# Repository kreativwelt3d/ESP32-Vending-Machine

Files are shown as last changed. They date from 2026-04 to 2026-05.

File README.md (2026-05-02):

# Vending Machine Firmware (ESP32-S3)

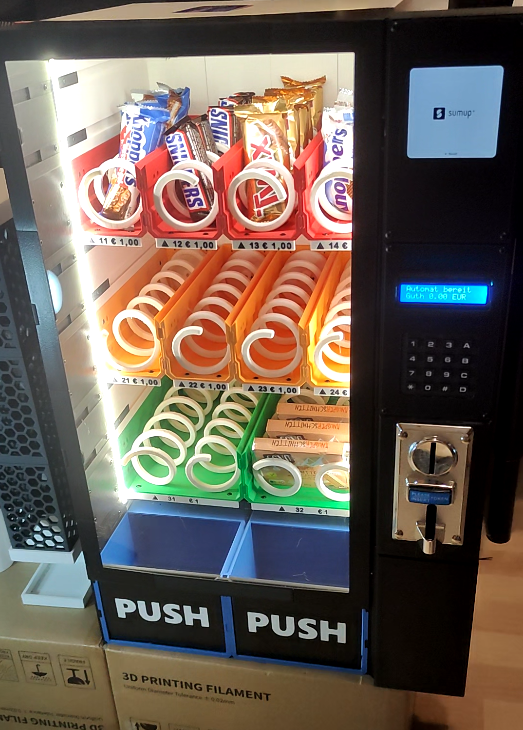
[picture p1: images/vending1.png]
Vending Machine


Language:

- [Deutsch](#deutsch)
- [English](#english)

Current firmware version in code: `1.7.0`

Ready-to-flash firmware releases are available here:

- https://github.com/kreativwelt3d/ESP32-Vending-Machine/releases

Kurzanleitung Flashen:

1. Fuer das [ESP Web Tool](https://espressif.github.io/esptool-js/) immer alle vier Dateien `bootloader.bin`, `partitions.bin`, `boot_app0.bin` und `firmware.bin` verwenden.
2. ESP32-S3 per USB verbinden.
3. Im ESP Web Tool mit `460800` Baud verbinden und `Flash Mode = DIO`, `Flash Frequency = 40m`, `Flash Size = 16MB` setzen.
4. Dateien mit diesen Offsets flashen: `bootloader.bin -> 0x0`, `partitions.bin -> 0x8000`, `boot_app0.bin -> 0xE000`, `firmware.bin -> 0x10000`.
5. Nach dem Flashen den ESP neu starten und den ersten Setup-Dialog auf dem LCD durchlaufen.

Quick flash guide:

1. For the [ESP Web Tool](https://espressif.github.io/esptool-js/), always use all four files: `bootloader.bin`, `partitions.bin`, `boot_app0.bin`, and `firmware.bin`.
2. Connect the ESP32-S3 via USB.
3. In the ESP Web Tool, connect with `460800` baud and set `Flash Mode = DIO`, `Flash Frequency = 40m`, and `Flash Size = 16MB`.
4. Flash the files with these offsets: `bootloader.bin -> 0x0`, `partitions.bin -> 0x8000`, `boot_app0.bin -> 0xE000`, `firmware.bin -> 0x10000`.
5. Reboot the ESP and complete the initial setup shown on the LCD.

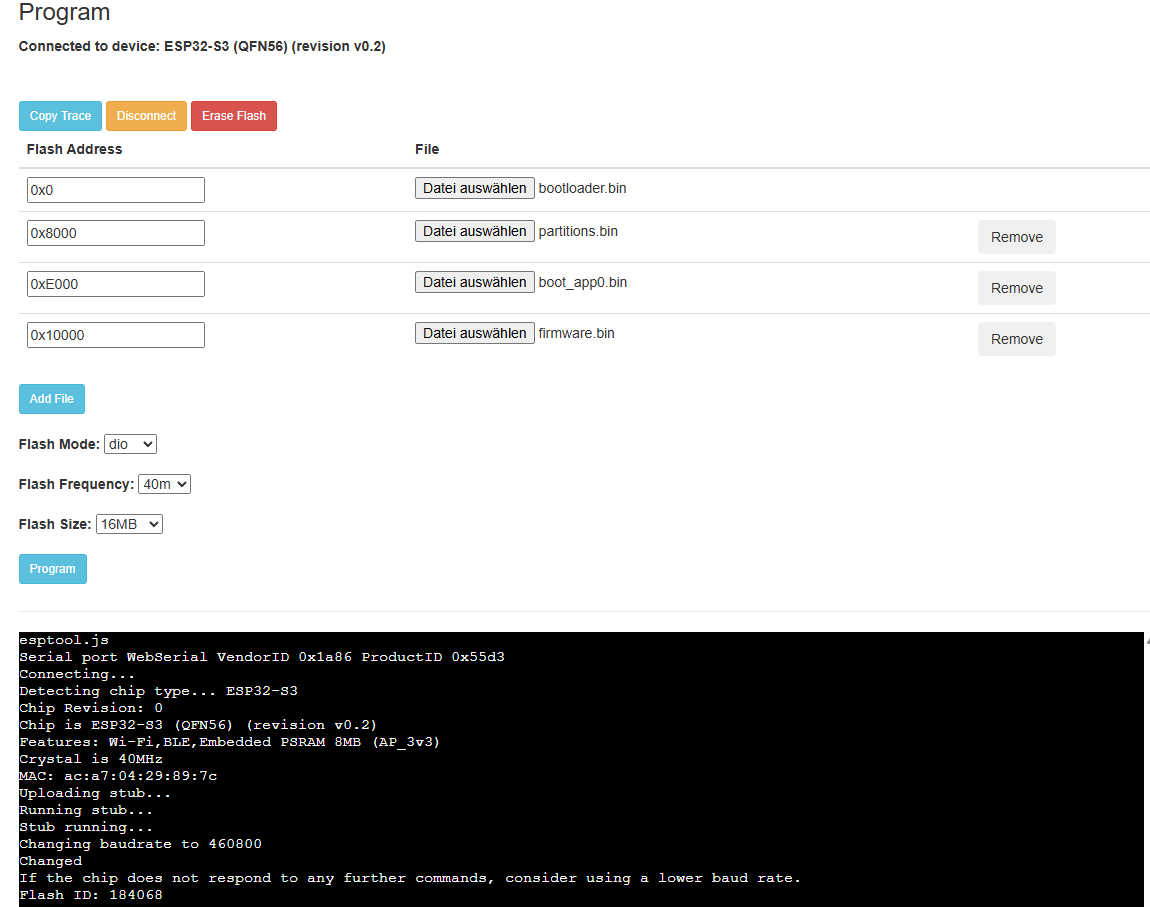
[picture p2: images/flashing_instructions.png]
Flashing instructions


---

## Deutsch

### Vorwort

Ein besonderer Dank geht an den Hauptschoepfer Martin auf MakerWorld fuer den grundlegenden Aufbau dieses Projekts und fuer das Bereitstellen der 3D-Druck-Dateien des Originalprojekts:

- https://makerworld.com/de/models/2380835-full-size-modular-vending-machine#profileId-2607127

Ausserdem begleitet eine TikTok-Videoreihe den kompletten Aufbau dieses Projekts. Die Links dazu koennen hier eingetragen werden:

Videoserie "Wir Drucken uns einen Verkaufsautomaten":
- Serien Start Teil 1: https://www.tiktok.com/@flo3137/video/7620130653631188246
- Aliexpress Lieferung + Unboxing Teil 2: https://www.tiktok.com/@flo3137/video/7622039398799904022
- Haupt aufbau des Automaten Teil 3: https://www.tiktok.com/@flo3137/video/7624063139864202518
- Elektronik Aufbau Teil 4: https://www.tiktok.com/@flo3137/video/7625582070978628867
- SumUP Mod + Finaler Teil: https://www.tiktok.com/@flo3137/video/7629085141201227031

Extra Videos:
- BL616 Münzprüfer Setup: https://www.tiktok.com/@flo3137/video/7628382295723887894

### Ueberblick

Diese Firmware steuert den Haupt-ESP eines Verkaufsautomaten. Der ESP32-S3 uebernimmt Anzeige, Tastenfeld, Muenzannahme, SD-Karte, WLAN/Weboberflaeche und die Kommunikation mit dem separaten Motor-ESP.

3D-Druck-Dateien und Hinweise zu den verfuegbaren Modifikationen findest du in [3DPrinting files/README.md](3DPrinting%20files/README.md).

### Funktionsumfang

- 4x4-Keypad fuer Bedienung und Service-Menue
- 16x2-LCD ueber I2C
- Erststart- und Service-Keypad-Setup zur Tasten-Zuordnung
- Muenzpruefer mit frei konfigurierbaren Puls/Wert-Mappings
- SD-Karte fuer Kassenbuch
- WLAN-Konfiguration
- Webserver fuer Konfiguration und Status
- Kommunikation mit separatem Motor-ESP per UART
- Ansteuerung von bis zu 24 Motoren ueber den separaten Motor-ESP
- Persistente Speicherung ueber Preferences (NVS)
- SumUp-Anbindung fuer Kartenzahlung
- Erstellung von Flash-Dateien fuer `esptool` und ESP Web Tool

### Hardware und Verdrahtung

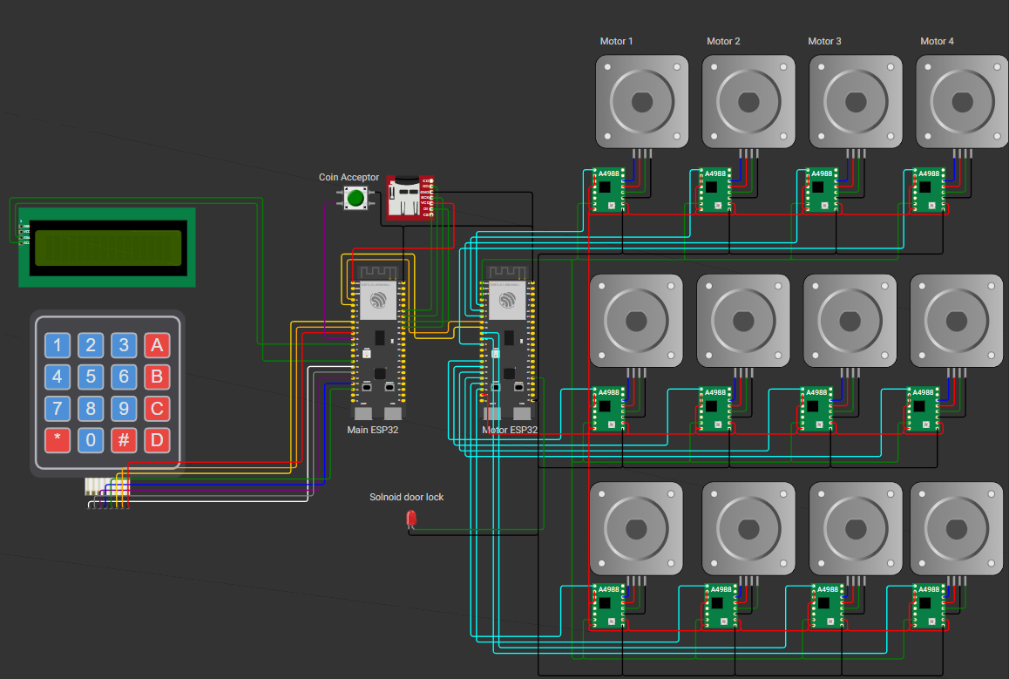
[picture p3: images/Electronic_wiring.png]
Aktuelle 5-Volt-Verdrahtung


*Aktuelle 5-Volt-Verdrahtung. Das Bild zeigt die komplette Verdrahtung aller Komponenten. Die 12V-Leitungen wurden bewusst weggelassen, um die Logik besser darzustellen.*

Alle aktuell in der Firmware belegten GPIOs:

| Funktion | Signal | GPIO |
|---|---|---|
| LCD I2C | SDA | `8` |
| LCD I2C | SCL | `9` |
| Keypad | Row 1 | `10` |
| Keypad | Row 2 | `11` |
| Keypad | Row 3 | `12` |
| Keypad | Row 4 | `13` |
| Keypad | Col 1 | `14` |
| Keypad | Col 2 | `15` |
| Keypad | Col 3 | `16` |
| Keypad | Col 4 | `17` |
| Muenzpruefer | Pulse input | `18` |
| Motor-ESP UART | TX vom Haupt-ESP | `4` |
| Motor-ESP UART | RX zum Haupt-ESP | `5` |
| SD-Karte SPI | SCK / CLK | `39` |
| SD-Karte SPI | MOSI / DI | `40` |
| SD-Karte SPI | MISO / DO | `41` |
| SD-Karte SPI | CS / SS | `42` |

Nicht aufgefuehrte GPIOs sind in der aktuellen Hauptplatinen-Firmware nicht belegt.

#### LCD

- Display: `16x2`
- I2C-Start im Code: `Wire.begin(8, 9)`
- Typische I2C-Adresse: `0x27`

Verdrahtung:

- `SDA -> GPIO 8`
- `SCL -> GPIO 9`
- `VCC -> 5V` oder `3.3V` je nach LCD-Backpack
- `GND -> GND`

Hinweis:

- Wenn das Display ueber I2C zu schwach leuchten sollte, kann zuerst der Kontrast ueber den Drehwiderstand am LCD-Backpack eingestellt werden.
- Falls das nicht ausreicht, kann statt `3.3V` auch `5V` fuer die Versorgung des Displays genutzt werden. Eventuell ist dann ein Level-Shifter zwischen `GPIO 8` und `GPIO 9` notwendig, um die ESP-Elektronik zu schuetzen.
- Die meisten LCD-Backpacks bringen diese Anpassung allerdings bereits von sich aus mit.

#### Keypad

Logische 4x4-Matrix:

| | Col 1 | Col 2 | Col 3 | Col 4 |
|---|---|---|---|---|
| Row 1 | 1 | 2 | 3 | A |
| Row 2 | 4 | 5 | 6 | B |
| Row 3 | 7 | 8 | 9 | C |
| Row 4 | * | 0 | # | D |

Physische Verdrahtung:

- `Row 1 -> GPIO 10`
- `Row 2 -> GPIO 11`
- `Row 3 -> GPIO 12`
- `Row 4 -> GPIO 13`
- `Col 1 -> GPIO 14`
- `Col 2 -> GPIO 15`
- `Col 3 -> GPIO 16`
- `Col 4 -> GPIO 17`

Hinweise:

- Beim ersten Start ohne gespeicherte Tasten-Zuordnung erscheint automatisch ein Keypad-Setup auf dem LCD.
- Das Setup kann spaeter erneut im Service-Menue ueber `Keypad Setup` gestartet werden.

#### Muenzpruefer

- Pulssignal-Eingang: `GPIO 18`
- Im Code als `INPUT_PULLUP` konfiguriert

Ein Video zum Einrichten des Muenzpruefers ist auf TikTok einsehbar:

- https://www.tiktok.com/@flo3137/video/7628382295723887894

Verdrahtung:

- `Signal / pulse out -> GPIO 18`
- `GND -> GND`

Hinweis:

- Wenn das Signal an `GPIO 18` zu schwach ist, kann es mit einem `10 kOhm`-Widerstand zwischen `5V` und `GPIO 18` verbessert werden.

#### SD-Karte

Die SD-Karte wird im SPI-Modus betrieben.

Aktuell funktionierende Verdrahtung:

- `CLK / SCK -> GPIO 39`
- `MOSI / DI -> GPIO 40`
- `MISO / DO -> GPIO 41`
- `CS / SS -> GPIO 42`
- `3V3 -> 3.3V`
- `GND -> GND`

Hinweise:

- Diese Belegung wurde erfolgreich getestet.
- Der testweise Pinblock `35/36/37/38` kann auf diesem Board zu Boot-Problemen fuehren.

#### Motor-ESP UART

Der Haupt-ESP kommuniziert mit dem separaten Motor-ESP ueber UART:

- `TX Haupt-ESP -> GPIO 4`
- `RX Haupt-ESP -> GPIO 5`
- Baudrate: `115200`

Verdrahtung:

- `GPIO 4` des Haupt-ESP an `RX` des Motor-ESP
- `GPIO 5` des Haupt-ESP an `TX` des Motor-ESP
- `GND` beider ESPs verbinden

Weitere Details zur Motor-Platine stehen in [motor_controller/README.md](motor_controller/README.md).

### Bedienkonzept

#### Wichtige Tasten

- `A` = Menue nach oben / Zeichensatz zurueck
- `B` = Menue nach unten / Zeichensatz weiter
- `C` = Zurueck / Abbrechen
- `D` = Bestaetigen / Enter
- `*` = Loeschen / Backspace
- `#` = regulaeres Eingabezeichen in Textfeldern

#### Service-Menue oeffnen

Wenn das Display auf "Automat bereit" steht, kann mit folgender nacheinander gedrücker Tasten `*` und `#` das Service-Menue geoeffnet werden.
Danach muss die Service-PIN eingegeben werden. Der standard Pin ist: `12345678`

#### Service-Menue

Aktuelle Menuepunkte:

1. `Info`
2. `WiFi`
3. `Admin PIN`
4. `Sprache`
5. `Keypad Setup`
6. `Tuer oeffnen`

#### WiFi-Text-Eingabe ueber das Keypad

Bei der Eingabe von `SSID` und `Passwort` wird eine Multi-Tap-Eingabe verwendet.

Bedienung:

- `A` = einen Zeichensatz zurueckschalten
- `B` = einen Zeichensatz weiterschalten
- `C` = Eingabe abbrechen und zurueck
- `D` = aktuelle Eingabe bestaetigen und speichern
- `*` = aktives Zeichen verwerfen oder letztes Zeichen loeschen
- Wenn dieselbe Zifferntaste mehrfach kurz hintereinander gedrueckt wird, wird durch die zugehoerigen Zeichen dieser Taste gewechselt
- Nach einer kurzen Pause wird das aktuell ausgewaehlte Zeichen uebernommen

Verfuegbare Zeichensaetze:

- `ABC` = Grossbuchstaben
- `abc` = Kleinbuchstaben
- `123` = Zahlen
- `Sym` = Sonderzeichen

Tastenbelegung:

- `0`
  Leerzeichen, `0` im Modus `ABC` und `abc`
  `0`, Leerzeichen, `@` im Modus `Sym`
  nur `0` im Modus `123`
- `1`
  `1 . - _` im Modus `ABC` und `abc`
  `1 .` im Modus `123`
  `. - _ /` im Modus `Sym`
- `2`
  `A B C 2` im Modus `ABC`
  `a b c 2` im Modus `abc`
  `2` im Modus `123`
  `# $ % &` im Modus `Sym`
- `3`
  `D E F 3` im Modus `ABC`
  `d e f 3` im Modus `abc`
  `3` im Modus `123`
  `* + = "` im Modus `Sym`
- `4`
  `G H I 4` im Modus `ABC`
  `g h i 4` im Modus `abc`
  `4` im Modus `123`
  `( ) , ;` im Modus `Sym`
- `5`
  `J K L 5` im Modus `ABC`
  `j k l 5` im Modus `abc`
  `5` im Modus `123`
  `: ! ? '` im Modus `Sym`
- `6`
  `M N O 6` im Modus `ABC`
  `m n o 6` im Modus `abc`
  `6` im Modus `123`
  `[ ] { }` im Modus `Sym`
- `7`
  `P Q R S 7` im Modus `ABC`
  `p q r s 7` im Modus `abc`
  `7` im Modus `123`
  `< > | \` im Modus `Sym`
- `8`
  `T U V 8` im Modus `ABC`
  `t u v 8` im Modus `abc`
  `8` im Modus `123`
  `^ ~ `` im Modus `Sym`
- `9`
  `W X Y Z 9` im Modus `ABC`
  `w x y z 9` im Modus `abc`
  `9` im Modus `123`
  `@` im Modus `Sym`
- `#`
  `#` in allen Zeichensaetzen

### Weboberflaeche

Der integrierte Webserver laeuft auf Port `80`.

Wichtige Bereiche:

- Uebersicht
- WiFi
- E-Mail
- SumUp
- Muenzen
- Schaechte
- Kassenbuch
- Tests

#### SumUp-Konfiguration

Im Tab `SumUp` werden die Parameter fuer die Kartenzahlung hinterlegt:

- `Aktiv`
- `Server Basis-URL`
- `Bearer Token`
- `Machine ID`
- `Currency`
- `Polling Intervall`
- `Timeout`

Beispiel fuer die `Server Basis-URL`:

```text
https://sumup.kreativwelt3d.de/sumup/public
```

Hinweise:

- Die Basis-URL muss auf den oeffentlich erreichbaren PHP-Bridge-Endpunkt zeigen.
- Der Bearer-Token schuetzt die Bridge-Endpunkte `/start` und `/status`.
- `Machine ID` muss mit dem Wert uebereinstimmen, den die Bridge fuer dieselbe Maschine erwartet.

#### SumUp API Bridge

Wenn du keine eigene SumUp API Bridge bauen und betreiben moechtest, kannst du die SumUp API Bridge auf meiner Webseite nutzen:

- https://sumup.kreativwelt3d.de/

Dieser Dienst kostet `5 EUR pro Monat` und kann nach der Anmeldung auf der Webseite ueber Stripe gebucht werden, wenn du keine eigene Bridge einsetzen willst.

Damit wird das Projekt mitfinanziert, und ich freue mich sehr, wenn du mit deiner Buchung dabei mithilfst.

Ueber den Dienst koennen dann beliebig viele SumUp-Terminals angebunden werden.

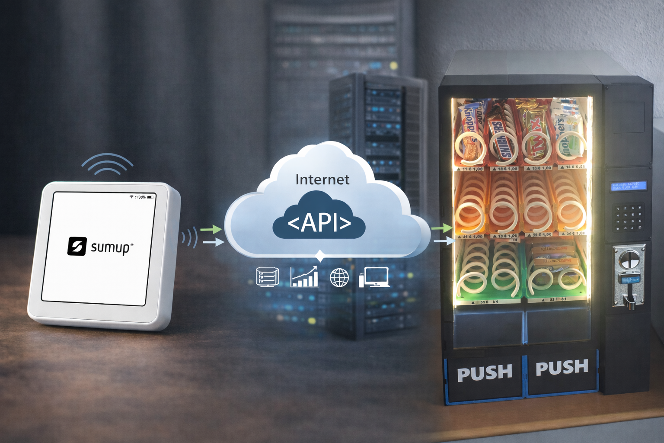
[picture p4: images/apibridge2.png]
SumUp API Bridge


#### Produkt- und Kartenzahlungsablauf

Die Produktauswahl am 4x4-Keypad erfolgt zweistufig:

- zuerst `Reihe 1-6`
- danach `Fach 1-8`

Beispiel:

- `1` dann `2` = Reihe 1, Fach 2

Wenn genuegend Guthaben vorhanden ist:

- Das Produkt wird direkt ausgegeben.

Wenn Guthaben fehlt und SumUp korrekt konfiguriert ist:

- Das LCD zeigt `Kartenzahlung->A`
- mit `A` wird die Kartenzahlung fuer genau diesen Artikel gestartet
- das LCD zeigt anschliessend `Terminal beachten`
- nach erfolgreicher Transaktion wird die Ware automatisch ausgegeben
- bei fehlgeschlagener oder abgebrochener Zahlung erfolgt keine Ausgabe

Wichtig:

- `A` startet im Normalmodus keine freie Betragsaufladung mehr.
- Die Kartenzahlung ist direkt an den ausgewaehlten Artikel gekoppelt.

#### Muenzkonfiguration

- Frei konfigurierbare Puls/Wert-Mappings
- Bis zu `20` Eintraege
- Weboberflaeche mit `Eintrag hinzufuegen` und `Eintrag entfernen`

#### Login

- Login mit Service-/Admin-PIN
- Session-Cookie: `ESPSESSIONID`

### Persistente Einstellungen

Namespace: `vending`

Gespeichert werden unter anderem:

- Admin-PIN
- WLAN-Daten
- Sprache
- Waehrung
- Keypad-Zuordnung
- Muenz-Mappings
- E-Mail-Konfiguration
- Schacht-Konfiguration

### Setup und Inbetriebnahme

1. Board `esp32-s3-devkitc-1-n16r8` in PlatformIO verwenden.
2. Firmware mit `platformio run` bauen.
3. Fuer das ESP Web Tool nicht die gemergte Datei `firmware-merged.bin` verwenden, sondern die vier Einzeldateien aus `.pio/build/esp32-s3-devkitc-1/`.
4. Im ESP Web Tool mit `460800` Baud verbinden und `Flash Mode = DIO`, `Flash Frequency = 40m`, `Flash Size = 16MB` setzen.
5. Dateien mit diesen Offsets flashen: `bootloader.bin -> 0x0`, `partitions.bin -> 0x8000`, `boot_app0.bin -> 0xE000`, `firmware.bin -> 0x10000`.
6. Seriellen Monitor mit `115200` Baud oeffnen.
7. Beim Erststart gegebenenfalls das Keypad-Setup auf dem LCD durchlaufen.
8. SD-Karte und WLAN pruefen.
9. Service-Menue und Weboberflaeche fuer weitere Konfiguration verwenden.

### Fehlersuche

#### SD-Karte wird nicht erkannt

- Verdrahtung fuer `GPIO 39/40/41/42` pruefen
- `3.3V` und `GND` pruefen
- Seriellen Monitor beobachten

#### Keypad reagiert falsch

- `Keypad Setup` im Service-Menue erneut ausfuehren
- Verdrahtung von Rows und Cols pruefen

#### Kein Zugriff auf die Webseite

- WLAN-Verbindung pruefen
- IP-Adresse im Info-Screen oder seriellen Monitor nachsehen
- Browser im selben Netzwerk verwenden

### Sicherheit und Grenzen

- Authentifizierung erfolgt ueber PIN und Session-Cookie
- Kein HTTPS/TLS in der aktuellen Firmware
- Fuer produktive Umgebungen sollte ein zusaetzliches Sicherheitskonzept ergaenzt werden

---

## English

### Preface

Special thanks go to Martin on MakerWorld, the main creator of the original build, for creating the foundation of this project and for providing the 3D printing files of the original project:

- https://makerworld.com/de/models/2380835-full-size-modular-vending-machine#profileId-2607127

In addition, a TikTok video series documents the complete build of this project the Series is held upon in German.Maybe i can add some english voiceover later on:

Videoseries "We print an vending machine":
- Series start part 1: https://www.tiktok.com/@flo3137/video/7620130653631188246
- Aliexpress delivered + Unboxing part 2: https://www.tiktok.com/@flo3137/video/7622039398799904022
- Main build of the vendingmachine part 3: https://www.tiktok.com/@flo3137/video/7624063139864202518
- Electronics part 4: https://www.tiktok.com/@flo3137/video/7625582070978628867
- SumUP Mod + Final part: https://www.tiktok.com/@flo3137/video/7629085141201227031

Extra Videos:
- BL616 Coin acceptor Setup: https://www.tiktok.com/@flo3137/video/7628382295723887894

### Overview

This firmware controls the main ESP of the vending machine. The ESP32-S3 handles the display, keypad, coin acceptor, SD card, Wi-Fi/web interface, and communication with the separate motor ESP.

3D printing files and notes about the available modifications can be found in [3DPrinting files/README.md](3DPrinting%20files/README.md).

### Features

- 4x4 keypad for normal operation and service menu
- 16x2 LCD via I2C
- Initial and service keypad setup for key mapping
- Coin acceptor with configurable pulse/value mappings
- SD card support for the cashbook
- Wi-Fi configuration
- Web server for configuration and status pages
- UART communication with a separate motor ESP
- Control of up to 24 motors through the separate motor ESP
- Persistent storage via Preferences (NVS)
- SumUp integration for card payments
- Automatic creation of flash files for `esptool` and ESP Web Tool

### Hardware and wiring

Current 5-volt wiring

*Current 5-volt wiring. The image shows the complete wiring of all components. The 12V lines were intentionally omitted to make the logic easier to understand.*

GPIOs currently used by the firmware:

| Function | Signal | GPIO |
|---|---|---|
| LCD I2C | SDA | `8` |
| LCD I2C | SCL | `9` |
| Keypad | Row 1 | `10` |
| Keypad | Row 2 | `11` |
| Keypad | Row 3 | `12` |
| Keypad | Row 4 | `13` |
| Keypad | Col 1 | `14` |
| Keypad | Col 2 | `15` |
| Keypad | Col 3 | `16` |
| Keypad | Col 4 | `17` |
| Coin acceptor | Pulse input | `18` |
| Motor ESP UART | TX from main ESP | `4` |
| Motor ESP UART | RX to main ESP | `5` |
| SD card SPI | SCK / CLK | `39` |
| SD card SPI | MOSI / DI | `40` |
| SD card SPI | MISO / DO | `41` |
| SD card SPI | CS / SS | `42` |

Unlisted GPIOs are currently unused by the main board firmware.

For the motor ESP pin mapping, see [motor_controller/README.md](motor_controller/README.md).

### User interaction

Important keys:

- `A` = menu up / previous character set
- `B` = menu down / next character set
- `C` = back / cancel
- `D` = confirm / enter
- `*` = delete / backspace
- `#` = regular input character in text fields

If the display shows "Machine ready" then the service menu is opened by pressing `*` and `#` quickly one after another, then entering the service PIN. The service pin is `12345678`

Current service menu items:

1. `Info`
2. `WiFi`
3. `Admin PIN`
4. `Language`
5. `Keypad Setup`
6. `Open door`

#### WiFi text input via keypad

When entering `SSID` and `password`, the firmware uses a multi-tap text input.

Controls:

- `A` = switch to the previous character set
- `B` = switch to the next character set
- `C` = cancel input and go back
- `D` = confirm and save the current input
- `*` = discard the active character or delete the last committed character
- Pressing the same number key multiple times quickly cycles through the characters assigned to that key
- After a short pause, the currently selected character is committed

Available character sets:

- `ABC` = uppercase letters
- `abc` = lowercase letters
- `123` = numbers
- `Sym` = symbols

Key mapping:

- `0`
  space, `0` in `ABC` and `abc`
  space, `0`, `@` in `Sym`
  only `0` in `123`
- `1`
  `1 . - _` in `ABC` and `abc`
  `1 .` in `123`
  `. - _ /` in `Sym`
- `2`
  `A B C 2` in `ABC`
  `a b c 2` in `abc`
  `2` in `123`
  `# $ % &` in `Sym`
- `3`
  `D E F 3` in `ABC`
  `d e f 3` in `abc`
  `3` in `123`
  `* + = "` in `Sym`
- `4`
  `G H I 4` in `ABC`
  `g h i 4` in `abc`
  `4` in `123`
  `( ) , ;` in `Sym`
- `5`
  `J K L 5` in `ABC`
  `j k l 5` in `abc`
  `5` in `123`
  `: ! ? '` in `Sym`
- `6`
  `M N O 6` in `ABC`
  `m n o 6` in `abc`
  `6` in `123`
  `[ ] { }` in `Sym`
- `7`
  `P Q R S 7` in `ABC`
  `p q r s 7` in `abc`
  `7` in `123`
  `< > | \` in `Sym`
- `8`
  `T U V 8` in `ABC`
  `t u v 8` in `abc`
  `8` in `123`
  `^ ~ `` in `Sym`
- `9`
  `W X Y Z 9` in `ABC`
  `w x y z 9` in `abc`
  `9` in `123`
  `@` in `Sym`
- `#`
  `#` in all character sets

### Web interface

The integrated web server runs on port `80`.

Main sections:

- Overview
- WiFi
- Email
- SumUp
- Coins
- Shafts
- Cashbook
- Tests

#### SumUp configuration

The `SumUp` tab contains the parameters for card payments:

- `Active`
- `Server base URL`
- `Bearer token`
- `Machine ID`
- `Currency`
- `Polling interval`
- `Timeout`

Example base URL:

```text
https://sumup.kreativwelt3d.de/sumup/public
```

#### SumUp API Bridge

If you do not want to build and host your own SumUp API bridge, you can use the SumUp API bridge on my website:

- https://sumup.kreativwelt3d.de/

This service costs `EUR 5 per month` and can be booked via Stripe after signing up on the website if you do not want to run your own bridge.

This helps fund the project, and I really appreciate everyone who supports it by subscribing to the service.

The service can be used to connect an unlimited number of SumUp terminals.

SumUp API Bridge

#### Product and card payment flow

Product selection on the 4x4 keypad is a two-step process:

- first `row 1-6`
- then `slot 1-8`

Example:

- `1` then `2` = row 1, slot 2

If enough credit is available:

- The product is dispensed immediately.

If there is not enough credit and SumUp is configured correctly:

- the LCD shows `Kartenzahlung->A`
- pressing `A` starts card payment for exactly that item
- the LCD then shows `Terminal beachten`
- after a successful transaction, the product is dispensed automatically
- no product is dispensed if the payment fails or is cancelled

### Persistent settings

Namespace: `vending`

Stored values include:

- admin PIN
- Wi-Fi settings
- language
- currency
- keypad mapping
- coin mappings
- email configuration
- shaft configuration

### Build and flashing

1. Use board `esp32-s3-devkitc-1-n16r8` in PlatformIO.
2. Build with `platformio run`.
3. For the ESP Web Tool, do not use the merged image `firmware-merged.bin`; use the four separate files from `.pio/build/esp32-s3-devkitc-1/` instead.
4. In the ESP Web Tool, connect with `460800` baud and set `Flash Mode = DIO`, `Flash Frequency = 40m`, and `Flash Size = 16MB`.
5. Flash the files with these offsets: `bootloader.bin -> 0x0`, `partitions.bin -> 0x8000`, `boot_app0.bin -> 0xE000`, `firmware.bin -> 0x10000`.
6. Open the serial monitor at `115200` baud.
7. Run the LCD keypad setup on first boot if needed.
8. Check SD card and Wi-Fi.
9. Use the service menu and web UI for further configuration.

### Troubleshooting

#### SD card is not detected

- Check wiring for `GPIO 39/40/41/42`
- Check `3.3V` and `GND`
- Watch the serial monitor output

#### Keypad behaves incorrectly

- Run `Keypad Setup` again from the service menu
- Check row and column wiring

#### Web interface is not reachable

- Check the Wi-Fi connection
- Look up the IP address on the info screen or in the serial monitor
- Make sure the browser is on the same network

### Security and limitations

- Authentication uses a PIN and session cookie
- No HTTPS/TLS in the current firmware
- A dedicated security concept is recommended for production environments

---

Notes:

- This README describes the main board firmware in `main_esp/src/sketch.ino`.
- The motor controller board has its own firmware and documentation in `motor_controller`.

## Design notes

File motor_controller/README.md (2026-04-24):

# Motor ESP Pinout

Language:

- [Deutsch](#deutsch)
- [English](#english)

---

## Deutsch

Diese Firmware in `src/main.cpp` ist fuer einen separaten ESP32-S3 als Motor-Controller gedacht.

Der Motor-ESP uebernimmt:

- 24 Stepper-Treiber ueber gemeinsame `STEP`-Leitung
- individuelle `ENABLE`-Leitungen pro Treiber
- Magnetschloss
- UART-Kommunikation mit dem Haupt-ESP

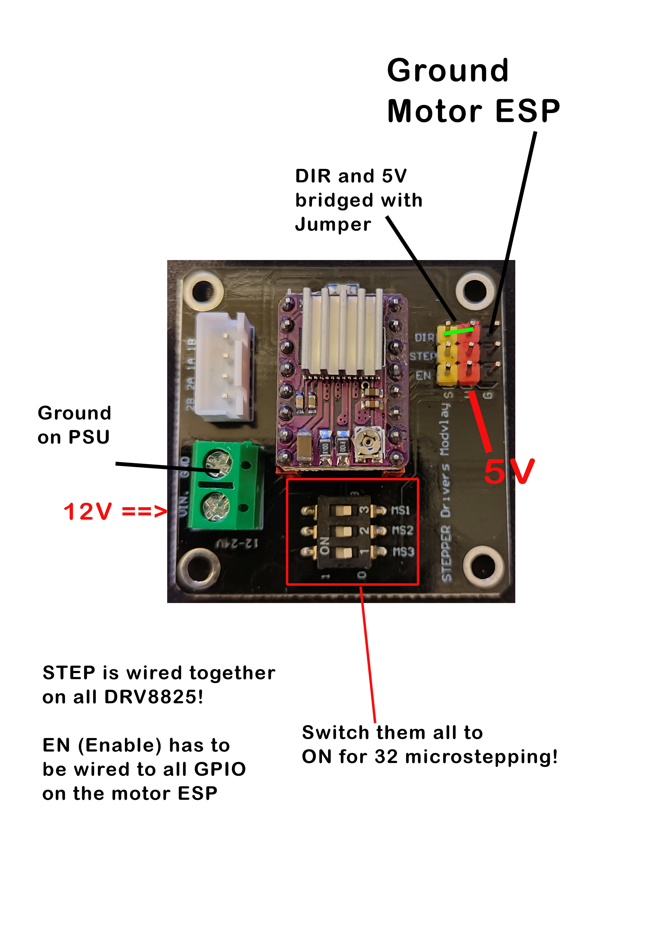
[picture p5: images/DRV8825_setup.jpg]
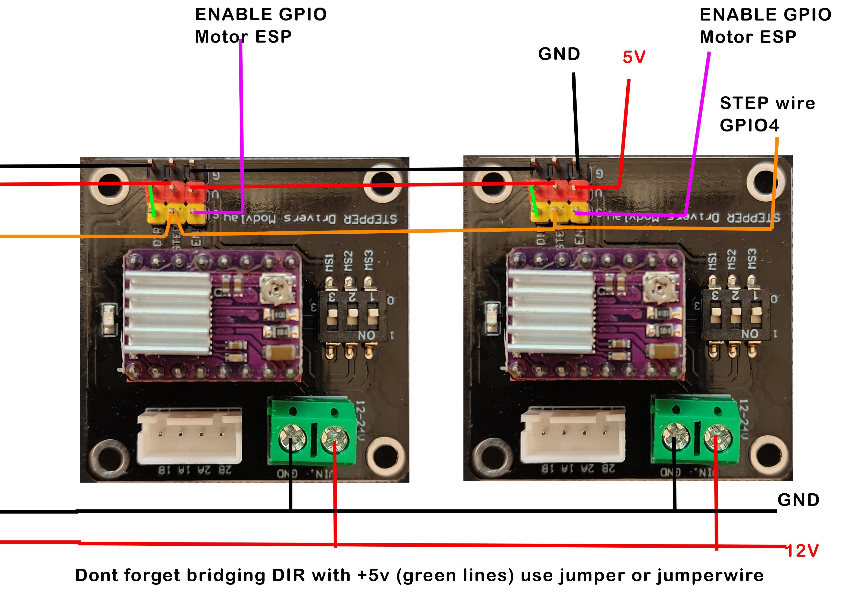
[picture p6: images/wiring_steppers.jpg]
  

Motor ESP wiring

## UART zum Haupt-ESP

Aktuelle Konfiguration im Sketch:

- Motor-ESP `RX`: `GPIO15`
- Motor-ESP `TX`: `GPIO16`
- Baudrate: `115200`

Verdrahtung:

- Haupt-ESP `TX` -> Motor-ESP `RX (GPIO15)`
- Haupt-ESP `RX` <- Motor-ESP `TX (GPIO16)`
- `GND` beider ESPs verbinden

## Stepper-Pins

Gemeinsame `STEP`-Leitung:

- `GPIO4`

`ENABLE`-Leitungen der 24 Motoren:

1. Motor 1: `GPIO5`
2. Motor 2: `GPIO6`
3. Motor 3: `GPIO7`
4. Motor 4: `GPIO8`
5. Motor 5: `GPIO9`
6. Motor 6: `GPIO10`
7. Motor 7: `GPIO11`
8. Motor 8: `GPIO12`
9. Motor 9: `GPIO13`
10. Motor 10: `GPIO14`
11. Motor 11: `GPIO17`
12. Motor 12: `GPIO18`
13. Motor 13: `GPIO1`
14. Motor 14: `GPIO2`
15. Motor 15: `GPIO38`
16. Motor 16: `GPIO39`
17. Motor 17: `GPIO40`
18. Motor 18: `GPIO41`
19. Motor 19: `GPIO42`
20. Motor 20: `GPIO47`
21. Motor 21: `GPIO48`
22. Motor 22: `GPIO19`
23. Motor 23: `GPIO20`
24. Motor 24: `GPIO3`

Logik:

- `ENABLE` aktiv: `LOW`
- `ENABLE` inaktiv: `HIGH`

## Magnetschloss

- Schloss-Pin: `GPIO21`
- aktiv/offen: `HIGH`
- inaktiv/geschlossen: `LOW`

Standard-Pulsdauer:

- `5000 ms`

## Hinweise zur Verdrahtung

- Alle DRV8825-Treiber muessen eine gemeinsame `GND` mit dem Motor-ESP haben.
- Die gemeinsame `STEP`-Leitung geht an alle Treiber parallel.
- Jeder Treiber bekommt seine eigene `ENABLE`-Leitung.
- Aktuelle Motor-zu-Pin-Zuordnung: Motor 1->GPIO5, Motor 2->GPIO6, Motor 3->GPIO7, Motor 4->GPIO8, Motor 5->GPIO9, Motor 6->GPIO10, Motor 7->GPIO11, Motor 8->GPIO12, Motor 9->GPIO13, Motor 10->GPIO14, Motor 11->GPIO17, Motor 12->GPIO18, Motor 13->GPIO1, Motor 14->GPIO2, Motor 15->GPIO38, Motor 16->GPIO39, Motor 17->GPIO40, Motor 18->GPIO41, Motor 19->GPIO42, Motor 20->GPIO47, Motor 21->GPIO48, Motor 22->GPIO19, Motor 23->GPIO20, Motor 24->GPIO3.
- Wenn `DIR` ebenfalls ueber den Motor-ESP laufen soll, muss der Sketch erweitert werden. Aktuell unterstuetzt der Motor-ESP nur `STEP + ENABLE` entsprechend dem bestehenden Projektansatz.

## Relevante Stellen im Code

- Pin-Konfiguration: `src/main.cpp`
- Protokollbeschreibung: `PROTOCOL.md`

---

## English

This firmware in `src/main.cpp` is intended for a separate ESP32-S3 used as the motor controller.

The motor ESP handles:

- 24 stepper drivers through a shared `STEP` line
- individual `ENABLE` lines for each driver
- magnetic lock
- UART communication with the main ESP

  

Motor ESP wiring

## UART to the main ESP

Current configuration in the sketch:

- Motor ESP `RX`: `GPIO15`
- Motor ESP `TX`: `GPIO16`
- Baud rate: `115200`

Wiring:

- Main ESP `TX` -> Motor ESP `RX (GPIO15)`
- Main ESP `RX` <- Motor ESP `TX (GPIO16)`
- Connect `GND` between both ESPs

## Stepper pins

Shared `STEP` line:

- `GPIO4`

`ENABLE` lines for the 24 motors:

1. Motor 1: `GPIO5`
2. Motor 2: `GPIO6`
3. Motor 3: `GPIO7`
4. Motor 4: `GPIO8`
5. Motor 5: `GPIO9`
6. Motor 6: `GPIO10`
7. Motor 7: `GPIO11`
8. Motor 8: `GPIO12`
9. Motor 9: `GPIO13`
10. Motor 10: `GPIO14`
11. Motor 11: `GPIO17`
12. Motor 12: `GPIO18`
13. Motor 13: `GPIO1`
14. Motor 14: `GPIO2`
15. Motor 15: `GPIO38`
16. Motor 16: `GPIO39`
17. Motor 17: `GPIO40`
18. Motor 18: `GPIO41`
19. Motor 19: `GPIO42`
20. Motor 20: `GPIO47`
21. Motor 21: `GPIO48`
22. Motor 22: `GPIO19`
23. Motor 23: `GPIO20`
24. Motor 24: `GPIO3`

Logic:

- `ENABLE` active: `LOW`
- `ENABLE` inactive: `HIGH`

## Magnetic lock

- Lock pin: `GPIO21`
- active/open: `HIGH`
- inactive/closed: `LOW`

Default pulse duration:

- `5000 ms`

## Wiring notes

- All DRV8825 drivers must share `GND` with the motor ESP.
- The shared `STEP` line goes to all drivers in parallel.
- Each driver gets its own `ENABLE` line.
- Current motor-to-pin mapping: Motor 1->GPIO5, Motor 2->GPIO6, Motor 3->GPIO7, Motor 4->GPIO8, Motor 5->GPIO9, Motor 6->GPIO10, Motor 7->GPIO11, Motor 8->GPIO12, Motor 9->GPIO13, Motor 10->GPIO14, Motor 11->GPIO17, Motor 12->GPIO18, Motor 13->GPIO1, Motor 14->GPIO2, Motor 15->GPIO38, Motor 16->GPIO39, Motor 17->GPIO40, Motor 18->GPIO41, Motor 19->GPIO42, Motor 20->GPIO47, Motor 21->GPIO48, Motor 22->GPIO19, Motor 23->GPIO20, Motor 24->GPIO3.
- If `DIR` should also be controlled by the motor ESP, the sketch needs to be extended. At the moment the motor ESP only supports `STEP + ENABLE` based on the current project design.

## Relevant code locations

- Pin configuration: `src/main.cpp`
- Protocol description: `PROTOCOL.md`

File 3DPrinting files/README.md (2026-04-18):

# 3D Printing Files

## Deutsch

Die 3D-Dateien in diesem Ordner sind Modifikationen und Erweiterungen fuer das offizielle MakerWorld-Projekt von Martin.

Das Originalprojekt findest du hier:

- https://makerworld.com/de/models/2380835-full-size-modular-vending-machine#profileId-2607127

Die auf MakerWorld gehosteten Modifikationen findest du hier:

- https://makerworld.com/de/models/2678974-sumup-solo-terminal-mod-esp23-new-housing#profileId-2966622

Ein weiteres MakerWorld-Projekt fuer die Modifikationen rund um den Motor-ESP und den Bereich unter dem Geraet findest du hier:

- https://makerworld.com/de/models/2624323-esp32-keypad-housing-backplate-modification#profileId-2897053

Bitte beachte, dass diese Dateien nicht das originale Basisprojekt ersetzen, sondern als angepasste Zusatz- oder Umbau-Teile dafuer gedacht sind. Die Modifikationen in diesem Repository und die MakerWorld-Versionen werden parallel gepflegt. Die Dateien aus dem Projekt fuer Motor-ESP und Unterseite sind ebenfalls in diesem GitHub-Repository enthalten.

## English

The 3D files in this folder are modifications and add-ons for Martin's official MakerWorld project.

You can find the original project here:

- https://makerworld.com/de/models/2380835-full-size-modular-vending-machine#profileId-2607127

The MakerWorld-hosted modifications are available here:

- https://makerworld.com/de/models/2678974-sumup-solo-terminal-mod-esp23-new-housing#profileId-2966622

Another MakerWorld project for the motor ESP modifications and the parts mounted underneath the machine is available here:

- https://makerworld.com/de/models/2624323-esp32-keypad-housing-backplate-modification#profileId-2897053

Please note that these files do not replace the original base project. They are intended as custom additional or modified parts for it. The modifications in this repository and the MakerWorld versions are maintained in parallel. The files from the motor ESP and bottom-side project are also included in this GitHub repository.

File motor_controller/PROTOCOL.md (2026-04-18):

# UART Protocol

Der Haupt-ESP bleibt Master. Der Motor-ESP fuehrt nur niederwertige Aktoren aus:

- 24 Stepper-Treiber ueber gemeinsame `STEP`-Leitung und individuelle `ENABLE`
- Magnetschloss

## Transport

- Physikalisch: UART
- Baudrate: `115200`
- Verdrahtung:
  - Haupt-ESP `TX` -> Motor-ESP `RX`
  - Haupt-ESP `RX` <- Motor-ESP `TX`
  - gemeinsame `GND`
- Nachrichtenformat: ASCII, eine Zeile pro Frame, `\n` als Abschluss

## Frame-Format

Request:

```text
@<id> <CMD> [args...]
```

Response:

```text
@<id> OK [payload...]
@<id> ERR <code> [details...]
```

Asynchrone Events:

```text
!READY fw=motor-esp-v2
!BUSY <id> <task>
!DONE <id>
!LOCK open duration_ms=<n>
```

Die `id` kommt vom Haupt-ESP und erlaubt Korrelation von Request und Response.

## Befehle

`PING`

```text
@1 PING
@1 OK PONG
```

`INFO`

```text
@2 INFO
@2 OK fw=motor-esp-v2 motors=24 step_pin=4 lock_pin=21
```

`STATUS`

```text
@3 STATUS
@3 OK busy=0 door=closed
```

`OFF`

```text
@4 OFF
@4 OK motors=off
```

`TEST <motor> <steps> <pulse_us>`

- `motor`: 1..24
- `steps`: 1..12000
- `pulse_us`: 100..5000

```text
@5 TEST 3 200 800
@5 OK motors=3 steps=200 pulse_us=800
```

`RUN <mask> <steps> <pulse_us>`

- `mask` ist eine Bitmaske fuer Motoren 1..24
- Bit 0 = Motor 1
- Bit 1 = Motor 2
- ...
- Bit 23 = Motor 24

Beispiel: Motor 9 und 10 gemeinsam

```text
@6 RUN 0x300 3200 800
@6 OK motors=9,10 steps=3200 pulse_us=800
```

Motor-zu-Pin-Zuordnung auf dem Motor-ESP:

- Motor 1=`GPIO5`, Motor 2=`GPIO6`, Motor 3=`GPIO7`, Motor 4=`GPIO8`
- Motor 5=`GPIO9`, Motor 6=`GPIO10`, Motor 7=`GPIO11`, Motor 8=`GPIO12`
- Motor 9=`GPIO13`, Motor 10=`GPIO14`, Motor 11=`GPIO17`, Motor 12=`GPIO18`
- Motor 13=`GPIO1`, Motor 14=`GPIO2`, Motor 15=`GPIO38`, Motor 16=`GPIO39`
- Motor 17=`GPIO40`, Motor 18=`GPIO41`, Motor 19=`GPIO42`, Motor 20=`GPIO47`
- Motor 21=`GPIO48`, Motor 22=`GPIO19`, Motor 23=`GPIO20`, Motor 24=`GPIO3`

`LOCK [duration_ms]`

- Standard ohne Argument: `5000`

```text
@7 LOCK 5000
!BUSY 7 LOCK
!LOCK open duration_ms=5000
@7 OK lock=closed
!DONE 7
```

## Fehlercodes

- `BAD_FRAME`
- `BAD_CMD`
- `BAD_ARGS`
- `BUSY`
- `BAD_MOTOR`
- `RUN_FAIL`
- `TEST_FAIL`
- `LOCK_FAIL`

## Architekturentscheidung

Die Schachtlogik bleibt auf dem Haupt-ESP:

- Zuordnung Schacht -> Motor(e)
- Preislogik
- Bestandslogik
- Webserver
- WLAN

Der Motor-ESP kennt nur generische Aktionen:

- einen oder mehrere Motoren mit Schrittzahl/Pulsweite fahren
- Magnetschloss pulsen

Dadurch bleibt der Motor-ESP einfach und testbar.

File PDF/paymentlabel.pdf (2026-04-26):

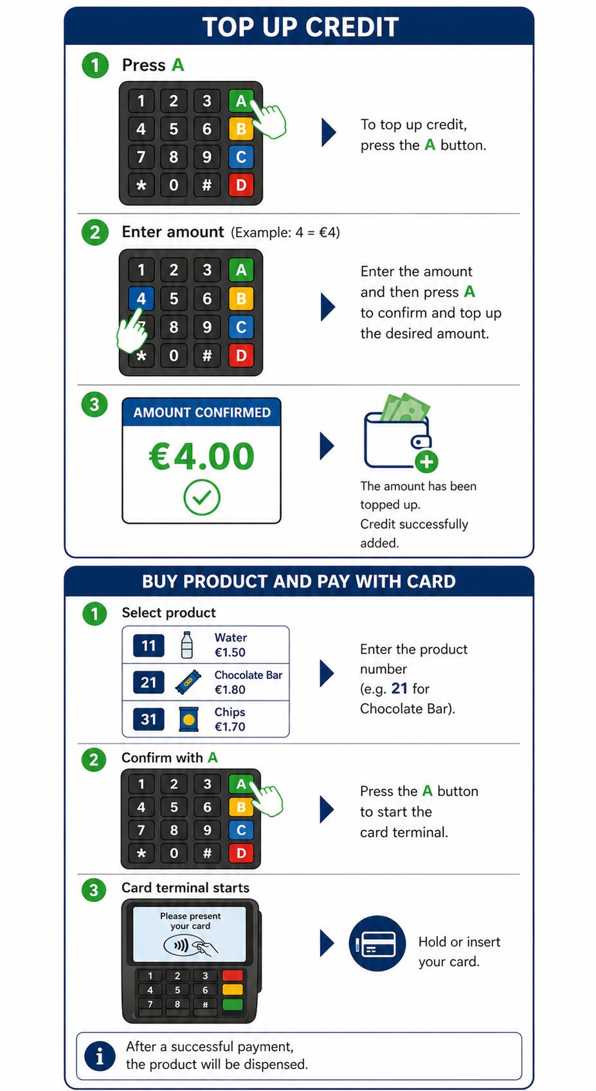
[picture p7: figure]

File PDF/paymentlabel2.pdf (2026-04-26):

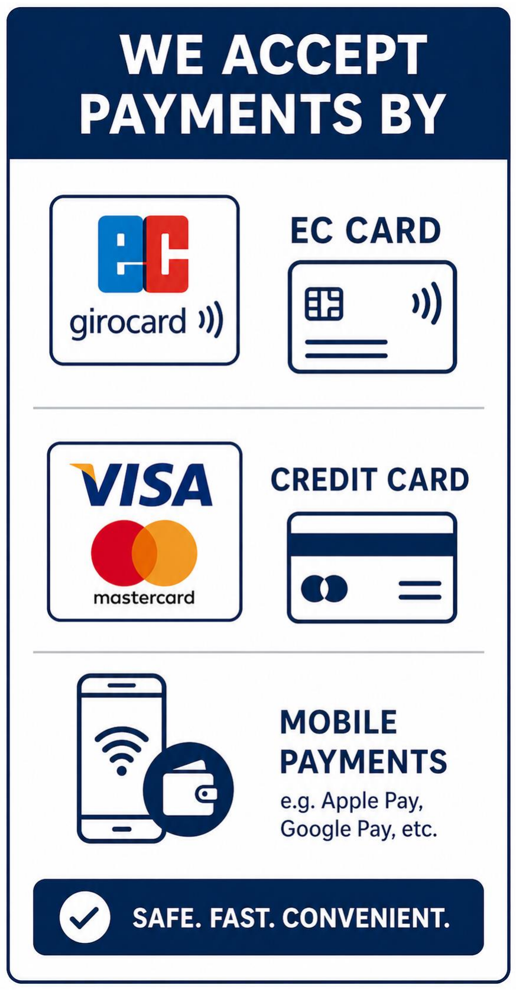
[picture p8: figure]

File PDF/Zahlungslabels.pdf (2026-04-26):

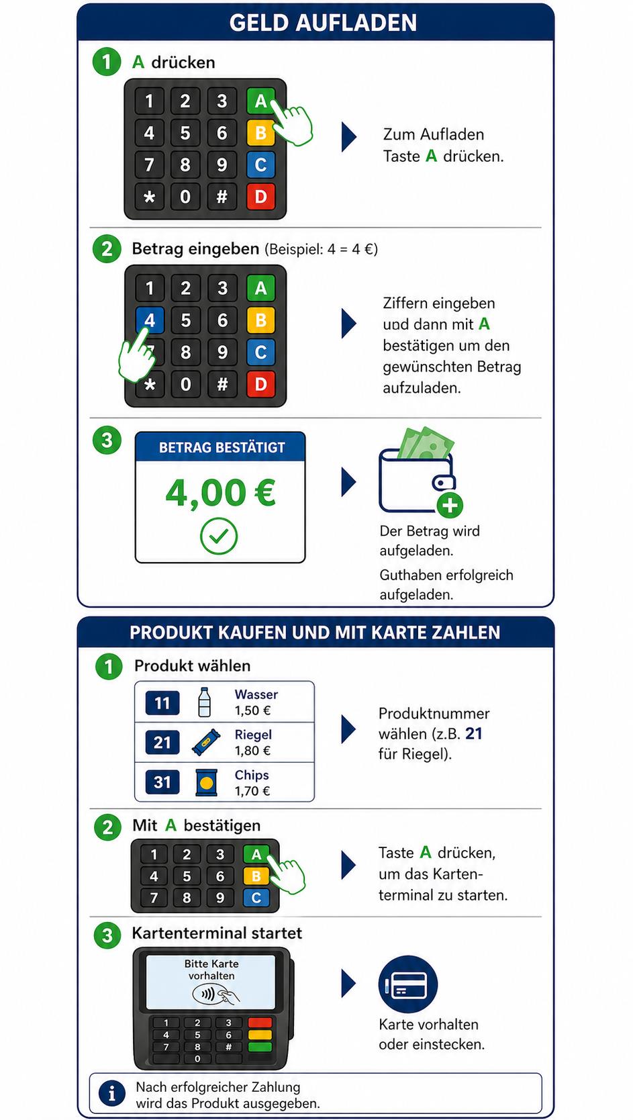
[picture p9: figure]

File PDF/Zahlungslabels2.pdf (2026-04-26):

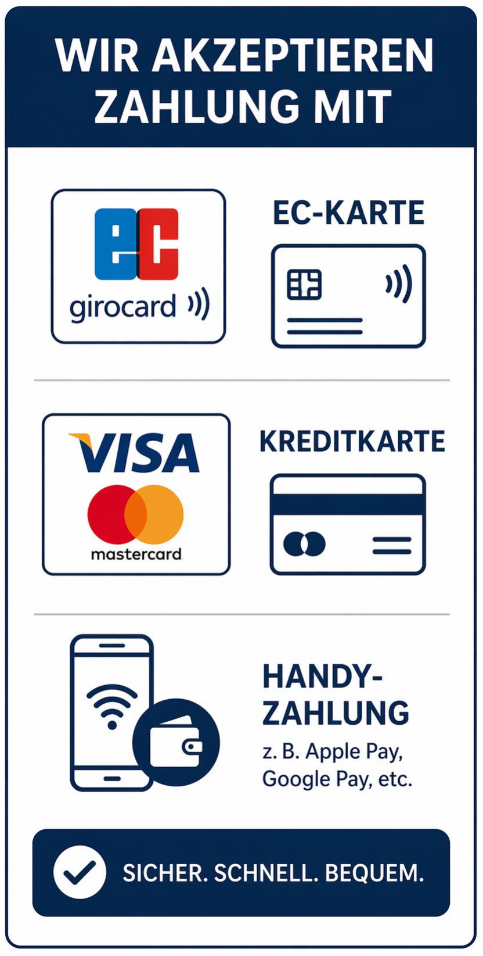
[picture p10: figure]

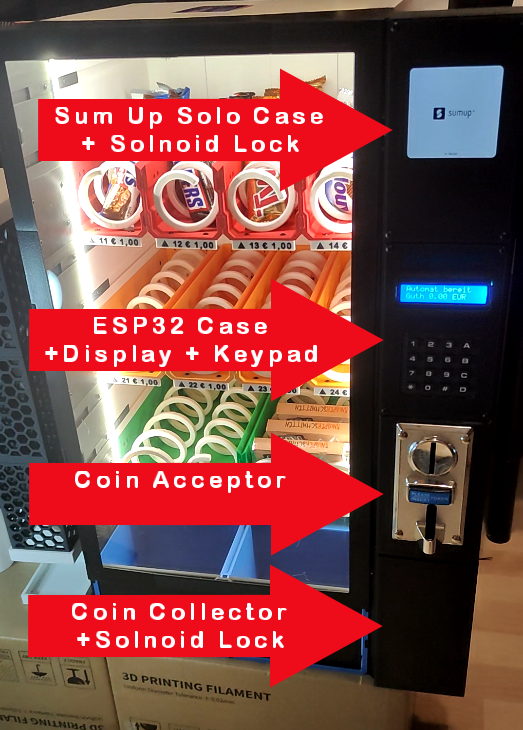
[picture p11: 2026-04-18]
images/vending6.png

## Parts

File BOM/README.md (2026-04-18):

# Bill of Materials (BOM)

Language:

- [Deutsch](#deutsch)
- [English](#english)

---

## Deutsch

Diese BOM beschreibt die wichtigsten Elektronik-Teile fuer das ESP32-Vending-Machine-Projekt.

Hinweis:

- Die unten aufgefuehrten Komponenten basieren auf der aktuell dokumentierten Hardware in diesem Repository.
- In der Spalte `Kauflink` koennen direkte Bezugsquellen eingetragen werden.
- Wo noch kein direkter Produktlink vorhanden ist, steht ein kurzer Kaufhinweis.

### Elektronik-Teile

| Bauteil | Menge | Beschreibung | Verwendung | Kauflink |
|---|---|---|---|---|
| ESP32-S3 Dev Board fuer Hauptsteuerung | 1 | Hauptcontroller fuer Display, Weboberflaeche, WLAN, SD-Karte, Muenzen und SumUp-Anbindung. Beim Kauf die Option `N16R8 KIT A` auswaehlen. | Haupt-ESP | https://de.aliexpress.com/item/1005008790807170.html |
| ESP32-S3 Dev Board fuer Motorsteuerung | 1 | Separater Controller fuer Motoren und Magnetschloss. Beim Kauf die Option `N16R8 KIT A` auswaehlen. | Motor-ESP | https://de.aliexpress.com/item/1005008790807170.html |
| 16x2 LCD mit I2C-Backpack | 1 | Anzeige fuer Menues, Status und Bedienung | Benutzeroberflaeche | https://de.aliexpress.com/item/1005007531187322.html |
| 4x4 Matrix-Keypad | 1 | Eingabe fuer Auswahl und Service-Menue | Benutzeroberflaeche | https://de.aliexpress.com/item/1005007728795501.html |
| Elektronischer Muenzpruefer | 1 | Gibt Pulse fuer erkannte Muenzen aus | Bezahlmodul | https://de.aliexpress.com/item/1005007423643042.html |
| MicroSD-Karte | 1 | Speicher fuer Kassenbuch und Daten | Speicher | Jede SD-Karte mit maximal `16 GB` funktioniert. |
| MicroSD-Kartenmodul oder integrierter SD-Anschluss | 1 | SPI-Anbindung der SD-Karte an den Haupt-ESP | Speicheranbindung | https://de.aliexpress.com/item/1005007211417449.html |
| DRV8825 Stepper-Treiber | 12 | Treiber fuer die einzelnen Ausgabemotoren | Motorsteuerung | https://de.aliexpress.com/item/1005009321177962.html |
| Stepper-Treiber-Erweiterungsplatine | 12 | Zum Stecken und Verkabeln der DRV8825-Treiber. Bitte die Variante mit der schwarzen Platine kaufen. | Motorsteuerung | https://de.aliexpress.com/item/1005006770144608.html |
| Schrittmotoren | 12 | Motoren fuer die Produktausgabe | Ausgabemechanik | https://de.aliexpress.com/item/1005003874936862.html |
| Magnetschloss / Solenoid Lock | 1 | Elektrische Verriegelung fuer die Tuer | Schloss | https://de.aliexpress.com/item/1005009789600010.html |
| SumUp Solo Terminal | 1 optional | Kartenzahlung ueber die SumUp API Bridge | Kartenzahlung | https://www.sumup.com/de-de/solo-kartenlesegeraet/ |
| 12V Netzteil, mindestens 4A | 1 | Versorgung fuer Motoren und leistungsstaerkere Verbraucher | Stromversorgung | Bitte ein hochwertiges Netzteil mit Hohlstecker waehlen. |
| LM2596 DC-DC Step-Down-Converter | 1 | Wandelt die Versorgungsspannung einzelner Baugruppen von `12V` auf `5V` | Stromversorgung | https://de.aliexpress.com/item/1005007003796615.html |
| 12V Relais-Modul | 1 | Schaltet die Versorgung fuer das Magnetschloss, wenn es benoetigt wird | Stromversorgung | https://de.aliexpress.com/item/1005007109343076.html |
| Anschlusskabel, Dupont-Kabel, Schraubklemmen | nach Bedarf | Verdrahtung aller Komponenten | Verkabelung | https://de.aliexpress.com/item/1005003219096948.html |
| Hohlstecker-Buchse | nach Bedarf | Anschluss fuer das 12V-Netzteil | Verkabelung | https://de.aliexpress.com/item/1005007870346260.html |

### Hinweise

- Die genaue Auswahl einzelner Module kann je nach verfuegbarer Hardware leicht variieren.
- In diesem Aufbau werden aktuell `12` DRV8825-Treiber und `12` Motoren genutzt, auch wenn die Firmware grundsaetzlich bis zu `24` Ausgaenge abbilden kann.
- Das SumUp-Terminal ist nur notwendig, wenn Kartenzahlung genutzt werden soll.
- Weitere technische Details findest du in [README.md](../README.md) und [motor_controller/README.md](../motor_controller/README.md).

---

## English

This BOM lists the main electronic parts used for the ESP32 Vending Machine project.

Note:

- The components below are based on the hardware currently documented in this repository.
- The `Purchase link` column can contain direct buying links or short buying notes.
- Where no direct product link is available, a short purchase note is used instead.

### Electronic parts

| Part | Qty | Description | Usage | Purchase link |
|---|-----|---|---|---|
| ESP32-S3 dev board for main controller | 1 | Main controller for display, web interface, Wi-Fi, SD card, coin handling and SumUp integration. Select the `N16R8 KIT A` option when ordering. | Main ESP | https://de.aliexpress.com/item/1005008790807170.html |
| ESP32-S3 dev board for motor controller | 1 | Separate controller for motors and the magnetic lock. Select the `N16R8 KIT A` option when ordering. | Motor ESP | https://de.aliexpress.com/item/1005008790807170.html |
| 16x2 LCD with I2C backpack | 1 | Display for menus, status information and user interaction | User interface | https://de.aliexpress.com/item/1005007531187322.html |
| 4x4 matrix keypad | 1 | Input device for selection and service menu | User interface | https://de.aliexpress.com/item/1005007728795501.html |
| Electronic coin acceptor | 1 | Outputs pulses for detected coins | Payment module | https://de.aliexpress.com/item/1005007423643042.html |
| MicroSD card | 1 | Storage for the cashbook and related data | Storage | Any SD card up to `16 GB` works. |
| MicroSD card module or integrated SD connector | 1 | SPI connection for the SD card on the main ESP | Storage interface | https://de.aliexpress.com/item/1005007211417449.html |
| DRV8825 stepper drivers | 12 | Drivers for the individual dispensing motors | Motor control | https://de.aliexpress.com/item/1005009321177962.html |
| Stepper driver expansion board | 12 | Used to plug in and wire the DRV8825 drivers. Buy the version with the black PCB. | Motor control | https://de.aliexpress.com/item/1005006770144608.html |
| Stepper motors | 12 | Motors used for product dispensing | Dispensing mechanism | https://de.aliexpress.com/item/1005003874936862.html |
| Magnetic lock / solenoid lock | 1 | Electric lock for the door | Lock | https://de.aliexpress.com/item/1005009789600010.html |
| SumUp Solo terminal | 1 optional | Card payment through the SumUp API bridge | Card payment | https://www.sumup.com/de-de/solo-kartenlesegeraet/ |
| 12V power supply, at least 4A | 1 | Power supply for motors and other higher-power loads | Power | Please choose a high-quality power supply with a barrel plug. |
| LM2596 DC-DC step-down converter | 1 | Converts the supply voltage for individual modules from `12V` to `5V` | Power | https://de.aliexpress.com/item/1005007003796615.html |
| 12V relay module | 1 | Switches power to the magnetic lock when needed | Power | https://de.aliexpress.com/item/1005007109343076.html |
| Wiring, Dupont cables, terminal blocks | as needed | Wiring for all components | Cabling | https://de.aliexpress.com/item/1005003219096948.html |
| Barrel jack socket | as needed | Connection for the 12V power supply | Cabling | https://de.aliexpress.com/item/1005007870346260.html |

### Notes

- The exact choice of modules may vary slightly depending on the hardware you use.
- This setup currently uses `12` DRV8825 drivers and `12` motors, even though the firmware can generally address up to `24` outputs.
- The SumUp terminal is only required if card payments are used.
- More technical details are available in [README.md](../README.md) and [motor_controller/README.md](../motor_controller/README.md).

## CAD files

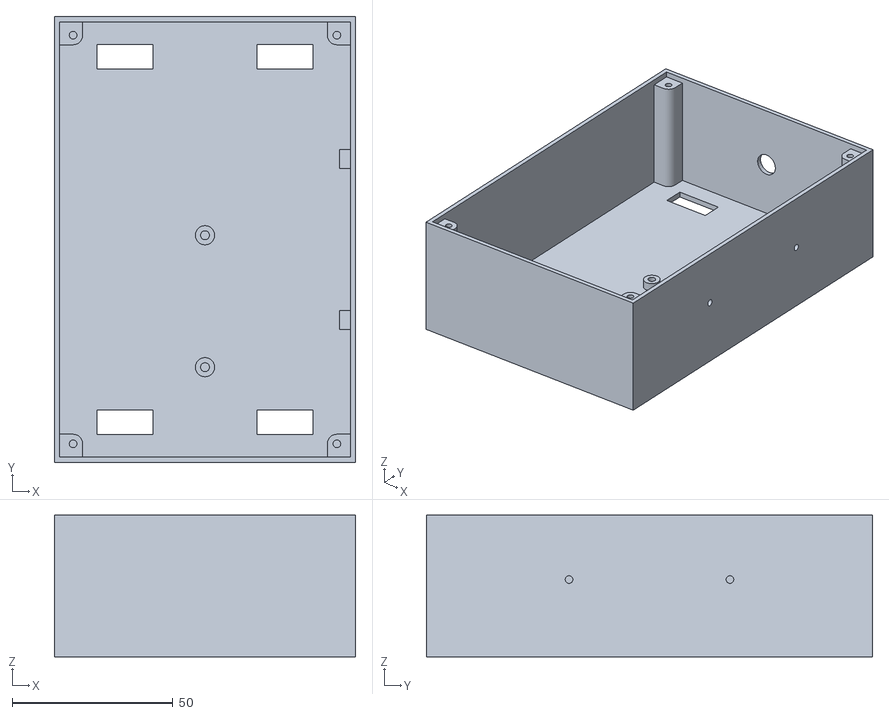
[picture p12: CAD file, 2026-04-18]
3DPrinting files/Keypad Body.stl
93.6 x 138.6 x 44.0

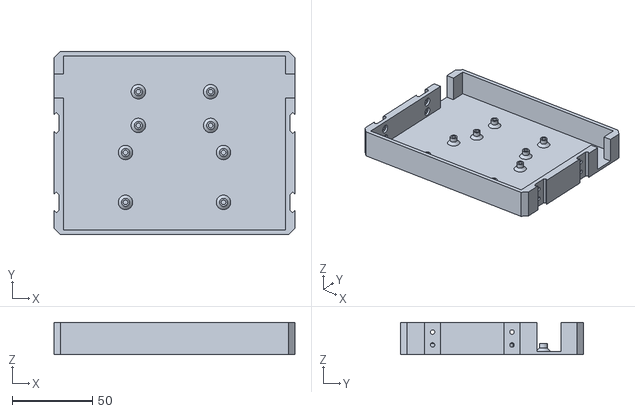
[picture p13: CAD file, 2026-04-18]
3DPrinting files/Motor ESP mod/Back Stand_opto_DC-DC.stl
150.0 x 114.0 x 20.0

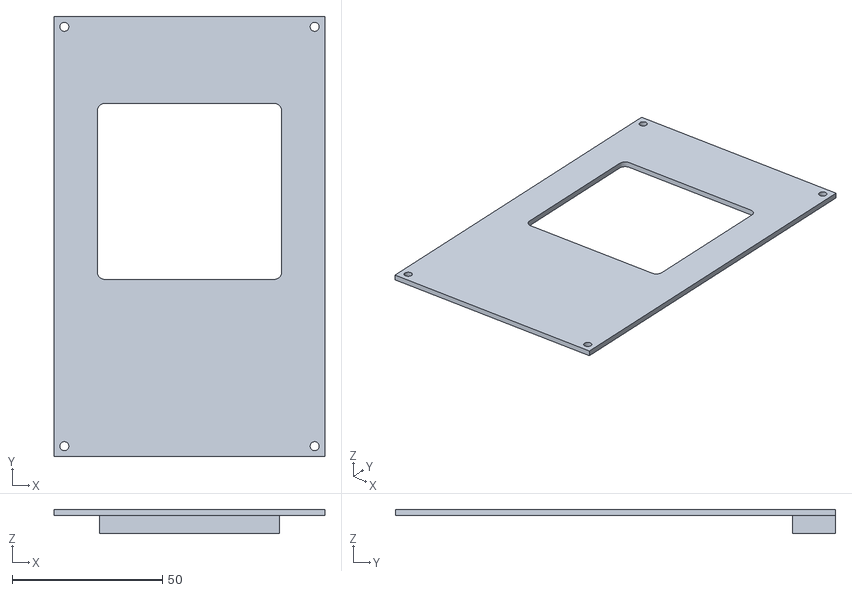
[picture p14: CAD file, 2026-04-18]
3DPrinting files/sumup_lid.stl
90.1 x 146.3 x 8.00

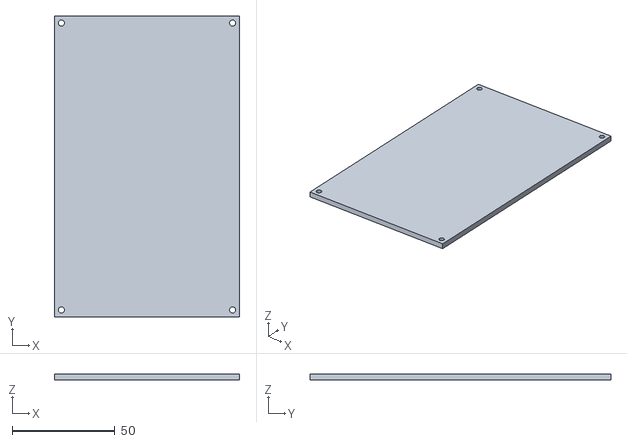
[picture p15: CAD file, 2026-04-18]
3DPrinting files/coin_acceptor_lid.stl
90.1 x 146.3 x 3.00

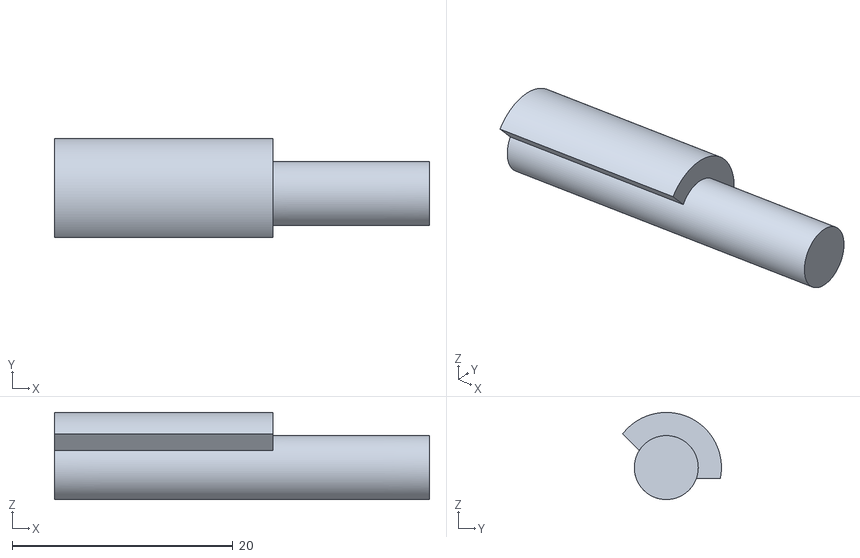
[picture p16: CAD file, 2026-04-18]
3DPrinting files/coin_collector_splint.stl
34.0 x 8.96 x 7.90

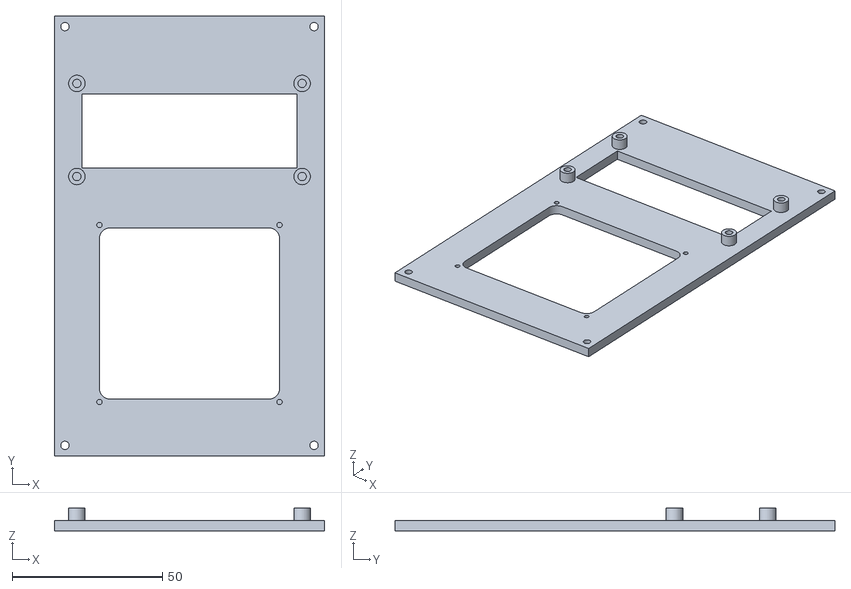
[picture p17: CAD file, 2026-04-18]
3DPrinting files/keypad+display lid.stl
90.0 x 146.5 x 7.50

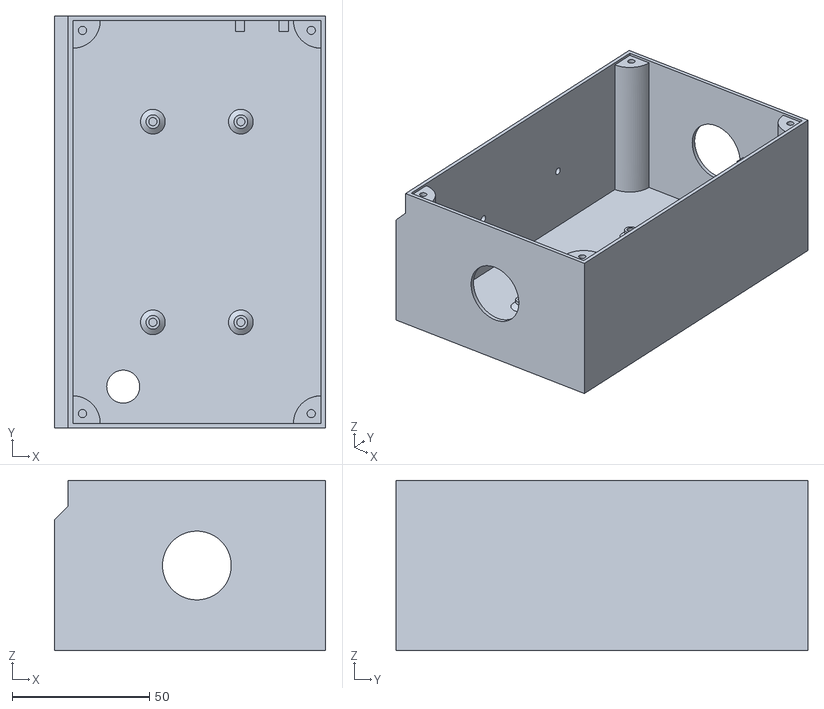
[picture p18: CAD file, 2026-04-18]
3DPrinting files/keypad+display+esp32+sdcard case.stl
98.6 x 149.8 x 62.0

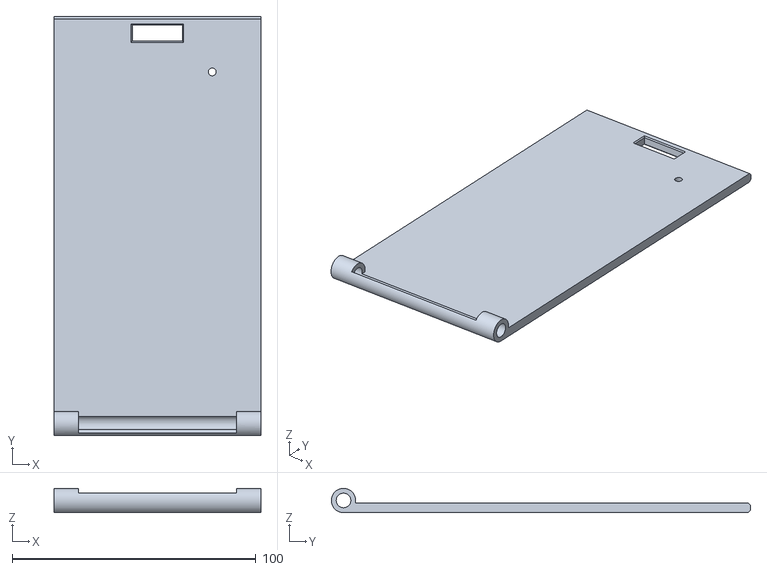
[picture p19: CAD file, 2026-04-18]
3DPrinting files/coin_collector_lid.stl
84.9 x 172.0 x 9.99

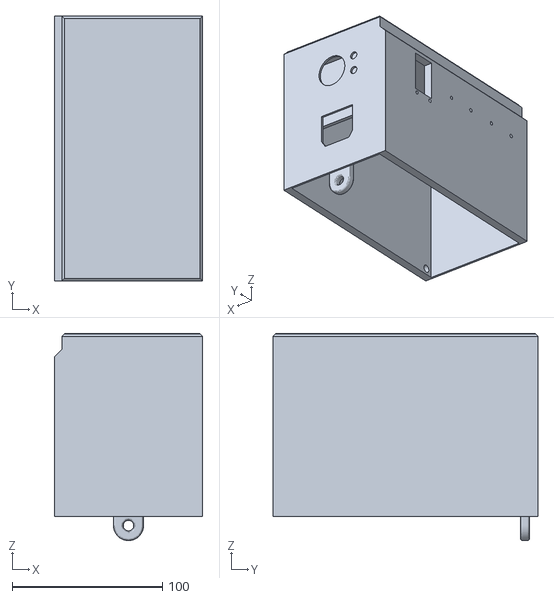
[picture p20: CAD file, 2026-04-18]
3DPrinting files/coin_collector.stl
98.6 x 176.5 x 138.0

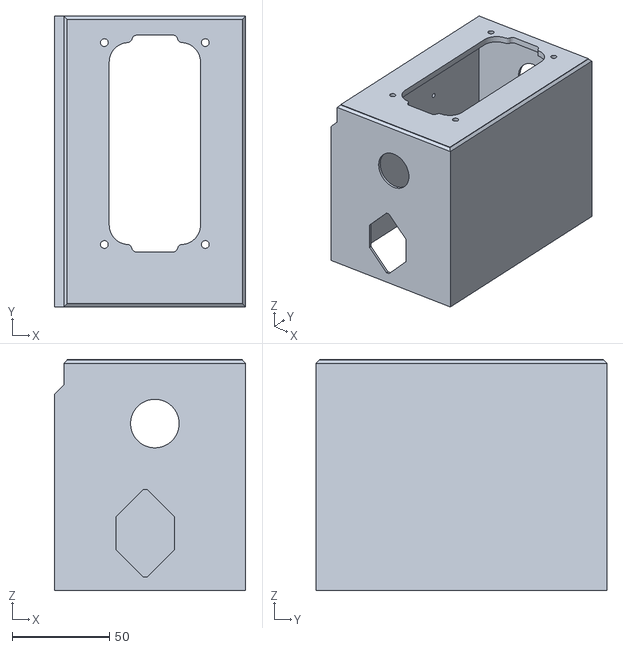
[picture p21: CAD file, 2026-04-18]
3DPrinting files/coin_acceptor_case.stl
98.6 x 149.8 x 119.0

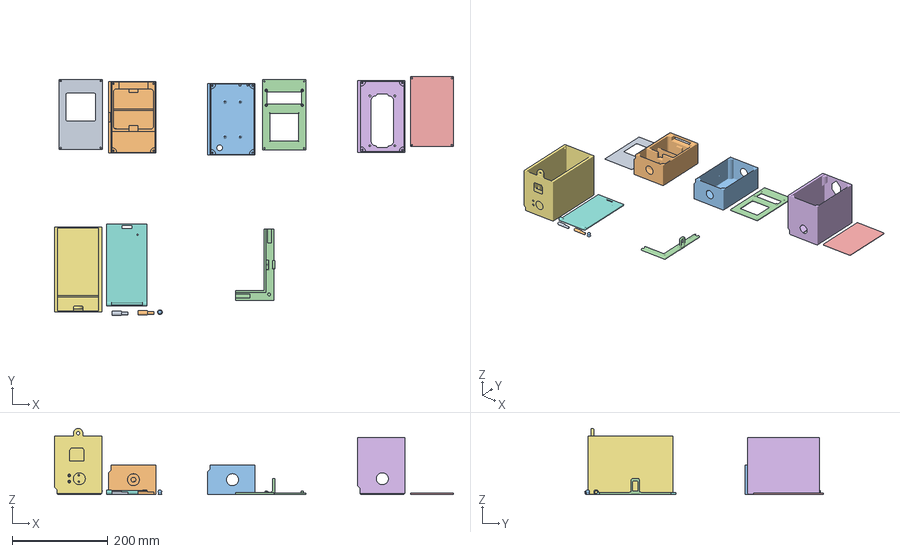
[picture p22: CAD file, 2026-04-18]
3DPrinting files/Vendingmachine SumUp mod with 2 solnoid locks.3mf
832.4 x 498.2 x 138.0 mm
sumup_lid.stl
Sumup_Terminal+Solnoid.stl
keypad+display+esp32+sdcard case.stl
keypad+display lid.stl
coin_acceptor_lid.stl
coin_acceptor_case.stl
coin_collector.stl
coin_collector_lid.stl
coin_collector_splint.stl x 2
coin_collector_lid_knob.stl
Door corner long Latch.stl

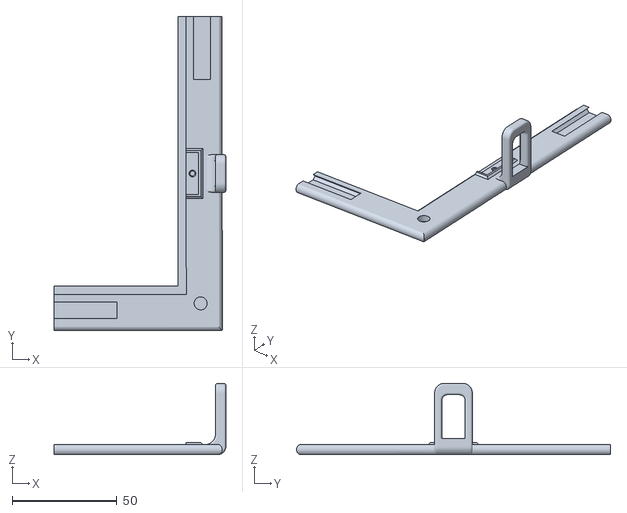
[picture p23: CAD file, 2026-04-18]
3DPrinting files/Door corner long Latch.stl
82.1 x 150.0 x 34.0

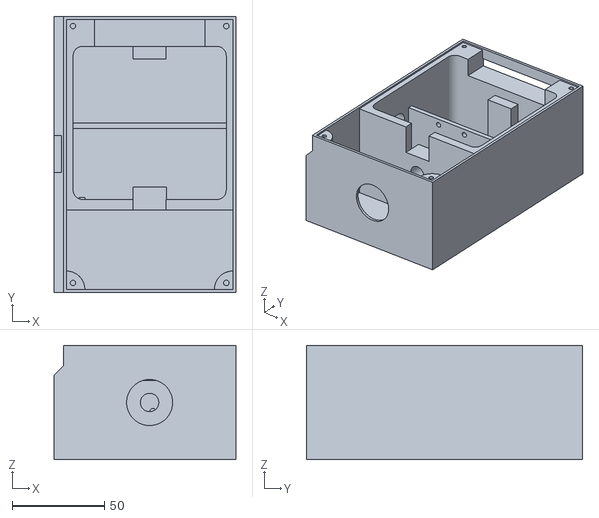
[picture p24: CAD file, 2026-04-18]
3DPrinting files/Sumup_Terminal+Solnoid.stl
98.6 x 149.8 x 62.0

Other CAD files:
3DPrinting files/Motor ESP mod/Keypad Body ESP32.stl
3DPrinting files/Motor ESP mod/Back Stand_ESP32.stl

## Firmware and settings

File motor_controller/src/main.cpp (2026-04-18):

#include <Arduino.h>
#include <esp_task_wdt.h>

namespace {

constexpr uint32_t kDebugBaud = 115200;
constexpr uint32_t kUartBaud = 115200;

// Adjust these pins to match the wiring between the two ESP32 boards.
constexpr int kMotorUartRxPin = 15;
constexpr int kMotorUartTxPin = 16;

constexpr int kStepperMotorCount = 24;
constexpr int kDefaultSharedStepPin = 4;
constexpr uint8_t kAllowedStepPins[] = {1, 2, 3, 4};
constexpr int kEnablePins[kStepperMotorCount] = {
    5,   // Motor 1
    6,   // Motor 2
    7,   // Motor 3
    8,   // Motor 4
    9,   // Motor 5
    10,  // Motor 6
    11,  // Motor 7
    12,  // Motor 8
    13,  // Motor 9
    14,  // Motor 10
    17,  // Motor 11
    18,  // Motor 12
    1,   // Motor 13
    2,   // Motor 14
    38,  // Motor 15
    39,  // Motor 16
    40,  // Motor 17
    41,  // Motor 18
    42,  // Motor 19
    47,  // Motor 20
    48,  // Motor 21
    19,  // Motor 22
    20,  // Motor 23
    3    // Motor 24
};

constexpr int kDoorLockPin = 21;
constexpr uint8_t kDoorLockUnlockLevel = HIGH;
constexpr uint8_t kDoorLockLockLevel = LOW;
constexpr uint32_t kDefaultDoorLockPulseMs = 5000;

constexpr uint16_t kMinPulseUs = 100;
constexpr uint16_t kMaxPulseUs = 5000;
constexpr uint16_t kMaxSteps = 12000;
constexpr uint32_t kMaxDoorPulseMs = 15000;
constexpr uint32_t kTaskWatchdogTimeoutSec = 8;
constexpr uint16_t kWatchdogFeedStepInterval = 32;

HardwareSerial MotorBus(1);
String rxLine;
bool controllerBusy = false;
uint32_t controllerBusyUntilMs = 0;
bool doorPulseActive = false;
uint8_t activeStepPin = kDefaultSharedStepPin;

String taskId = "";

void serviceWatchdog() {
  esp_task_wdt_reset();
  yield();
}

bool parseUint32Token(const String& token, uint32_t& value) {
  if (token.length() == 0) {
    return false;
  }

  char* endPtr = nullptr;
  unsigned long parsed = strtoul(token.c_str(), &endPtr, 0);
  if (endPtr == nullptr || *endPtr != '\0') {
    return false;
  }

  value = static_cast<uint32_t>(parsed);
  return true;
}

String nextToken(String& line) {
  line.trim();
  int split = line.indexOf(' ');
  if (split < 0) {
    String token = line;
    line = "";
    return token;
  }

  String token = line.substring(0, split);
  line.remove(0, split + 1);
  line.trim();
  return token;
}

void sendReply(const String& id, const String& status, const String& payload = "") {
  String line = "@";
  line += id;
  line += " ";
  line += status;
  if (payload.length() > 0) {
    line += " ";
    line += payload;
  }
  MotorBus.println(line);
  Serial.println("UART> " + line);
}

void sendEvent(const String& event, const String& payload = "") {
  String line = "!";
  line += event;
  if (payload.length() > 0) {
    line += " ";
    line += payload;
  }
  MotorBus.println(line);
  Serial.println("UART> " + line);
}

void disableAllMotors() {
  for (int i = 0; i < kStepperMotorCount; i++) {
    digitalWrite(kEnablePins[i], HIGH);
  }
}

bool isValidMotorIndex(uint32_t index) {
  return index >= 1 && index <= static_cast<uint32_t>(kStepperMotorCount);
}

bool isValidStepPin(uint8_t pin) {
  bool allowed = false;
  const int allowedCount = sizeof(kAllowedStepPins) / sizeof(kAllowedStepPins[0]);
  for (int i = 0; i < allowedCount; i++) {
    if (kAllowedStepPins[i] == pin) {
      allowed = true;
      break;
    }
  }
  if (!allowed) {
    return false;
  }
  if (pin == static_cast<uint8_t>(kMotorUartRxPin) || pin == static_cast<uint8_t>(kMotorUartTxPin) || pin == static_cast<uint8_t>(kDoorLockPin)) {
    return false;
  }
  for (int i = 0; i < kStepperMotorCount; i++) {
    if (pin == static_cast<uint8_t>(kEnablePins[i])) {
      return false;
    }
  }
  return true;
}

void beginTask(const String& id, const String& description) {
  controllerBusy = true;
  taskId = id;
  Serial.println("TASK START " + id + " " + description);
  sendEvent("BUSY", id + " " + description);
}

void finishTaskOk(const String& payload = "") {
  controllerBusy = false;
  controllerBusyUntilMs = 0;
  String currentTask = taskId;
  taskId = "";
  sendReply(currentTask, "OK", payload);
  sendEvent("DONE", currentTask);
}

void finishTaskErr(const String& code, const String& message) {
  controllerBusy = false;
  controllerBusyUntilMs = 0;
  String currentTask = taskId;
  taskId = "";
  sendReply(currentTask, "ERR", code + " " + message);
  sendEvent("DONE", currentTask);
}

bool runMotorMask(uint32_t motorMask, uint16_t steps, uint16_t pulseUs, uint8_t stepPin, String& message) {
  if (motorMask == 0) {
    message = "EMPTY_MASK";
    return false;
  }
  if (steps == 0 || steps > kMaxSteps) {
    message = "BAD_STEPS";
    return false;
  }
  if (pulseUs < kMinPulseUs || pulseUs > kMaxPulseUs) {
    message = "BAD_PULSE";
    return false;
  }
  if (!isValidStepPin(stepPin)) {
    message = "BAD_STEP_PIN";
    return false;
  }

  disableAllMotors();
  int enabledCount = 0;
  String motors = "";

  for (int i = 0; i < kStepperMotorCount; i++) {
    if ((motorMask & (1UL << i)) == 0) {
      continue;
    }
    digitalWrite(kEnablePins[i], LOW);
    if (enabledCount > 0) {
      motors += ",";
    }
    motors += String(i + 1);
    enabledCount++;
  }

  if (enabledCount == 0) {
    message = "EMPTY_MASK";
    return false;
  }

  pinMode(stepPin, OUTPUT);
  digitalWrite(stepPin, LOW);
  activeStepPin = stepPin;

  delay(2);
  for (uint16_t i = 0; i < steps; i++) {
    digitalWrite(stepPin, HIGH);
    delayMicroseconds(pulseUs);
    digitalWrite(stepPin, LOW);
    delayMicroseconds(pulseUs);
    if ((i % kWatchdogFeedStepInterval) == 0) {
      serviceWatchdog();
    }
  }

  disableAllMotors();

  message = "motors=" + motors + " steps=" + String(steps) + " pulse_us=" + String(pulseUs) + " step_pin=" + String(stepPin);
  return true;
}

bool startDoorPulse(uint32_t durationMs) {
  if (durationMs == 0 || durationMs > kMaxDoorPulseMs) {
    return false;
  }

  digitalWrite(kDoorLockPin, kDoorLockUnlockLevel);
  controllerBusy = true;
  taskId = taskId.length() > 0 ? taskId : "0";
  controllerBusyUntilMs = millis() + durationMs;
  doorPulseActive = true;
  return true;
}

void completeDoorPulseIfDue() {
  if (!doorPulseActive) {
    return;
  }

  if (static_cast<int32_t>(millis() - controllerBusyUntilMs) < 0) {
    return;
  }

  digitalWrite(kDoorLockPin, kDoorLockLockLevel);
  doorPulseActive = false;
  finishTaskOk("lock=closed");
}

void handlePing(const String& id) {
  sendReply(id, "OK", "PONG");
}

void handleInfo(const String& id) {
  String payload = "fw=motor-esp-v2 motors=" + String(kStepperMotorCount) +
                   " step_pin=" + String(activeStepPin) +
                   " lock_pin=" + String(kDoorLockPin);
  sendReply(id, "OK", payload);
}

void handleStatus(const String& id) {
  String payload = "busy=" + String(controllerBusy ? 1 : 0) +
                   " door=" + String(doorPulseActive ? "open" : "closed");
  sendReply(id, "OK", payload);
}

void handleMotorsOff(const String& id) {
  disableAllMotors();
  sendReply(id, "OK", "motors=off");
}

void handleRun(const String& id, String args) {
  uint32_t mask = 0;
  uint32_t steps = 0;
  uint32_t pulseUs = 0;
  uint32_t stepPin = activeStepPin;
  if (!parseUint32Token(nextToken(args), mask) ||
      !parseUint32Token(nextToken(args), steps) ||
      !parseUint32Token(nextToken(args), pulseUs)) {
    sendReply(id, "ERR", "BAD_ARGS usage=RUN mask steps pulse_us [step_pin]");
    return;
  }
  String stepPinToken = nextToken(args);
  if (stepPinToken.length() > 0 && !parseUint32Token(stepPinToken, stepPin)) {
    sendReply(id, "ERR", "BAD_ARGS usage=RUN mask steps pulse_us [step_pin]");
    return;
  }

  beginTask(id, "RUN");
  String message;
  if (!runMotorMask(mask, static_cast<uint16_t>(steps), static_cast<uint16_t>(pulseUs), static_cast<uint8_t>(stepPin), message)) {
    finishTaskErr("RUN_FAIL", message);
    return;
  }
  finishTaskOk(message);
}

void handleTest(const String& id, String args) {
  uint32_t motor = 0;
  uint32_t steps = 0;
  uint32_t pulseUs = 0;
  uint32_t stepPin = activeStepPin;
  if (!parseUint32Token(nextToken(args), motor) ||
      !parseUint32Token(nextToken(args), steps) ||
      !parseUint32Token(nextToken(args), pulseUs)) {
    sendReply(id, "ERR", "BAD_ARGS usage=TEST motor steps pulse_us [step_pin]");
    return;
  }
  String stepPinToken = nextToken(args);
  if (stepPinToken.length() > 0 && !parseUint32Token(stepPinToken, stepPin)) {
    sendReply(id, "ERR", "BAD_ARGS usage=TEST motor steps pulse_us [step_pin]");
    return;
  }
  if (!isValidMotorIndex(motor)) {
    sendReply(id, "ERR", "BAD_MOTOR");
    return;
  }

  beginTask(id, "TEST");
  String message;
  uint32_t mask = 1UL << (motor - 1);
  if (!runMotorMask(mask, static_cast<uint16_t>(steps), static_cast<uint16_t>(pulseUs), static_cast<uint8_t>(stepPin), message)) {
    finishTaskErr("TEST_FAIL", message);
    return;
  }
  finishTaskOk(message);
}

void handleLock(const String& id, String args) {
  uint32_t durationMs = kDefaultDoorLockPulseMs;
  String first = nextToken(args);
  if (first.length() > 0 && !parseUint32Token(first, durationMs)) {
    sendReply(id, "ERR", "BAD_ARGS usage=LOCK [duration_ms]");
    return;
  }

  beginTask(id, "LOCK");
  if (!startDoorPulse(durationMs)) {
    finishTaskErr("LOCK_FAIL", "BAD_DURATION");
    return;
  }
  sendEvent("LOCK", "open duration_ms=" + String(durationMs));
}

void handleCommand(String line) {
  line.trim();
  if (line.length() == 0) {
    return;
  }

  Serial.println("UART< " + line);

  String frame = line;
  String first = nextToken(frame);
  if (!first.startsWith("@")) {
    MotorBus.println("@0 ERR BAD_FRAME expected=@id CMD");
    return;
  }

  String id = first.substring(1);
  String cmd = nextToken(frame);
  cmd.toUpperCase();

  if (id.length() == 0 || cmd.length() == 0) {
    sendReply(id.length() > 0 ? id : "0", "ERR", "BAD_FRAME");
    return;
  }

  if (controllerBusy) {
    sendReply(id, "ERR", "BUSY active=" + taskId);
    return;
  }

  if (cmd == "PING") {
    handlePing(id);
  } else if (cmd == "INFO") {
    handleInfo(id);
  } else if (cmd == "STATUS") {
    handleStatus(id);
  } else if (cmd == "OFF") {
    handleMotorsOff(id);
  } else if (cmd == "RUN") {
    handleRun(id, frame);
  } else if (cmd == "TEST") {
    handleTest(id, frame);
  } else if (cmd == "LOCK") {
    handleLock(id, frame);
  } else {
    sendReply(id, "ERR", "BAD_CMD");
  }
}

void pollMotorBus() {
  while (MotorBus.available() > 0) {
    char c = static_cast<char>(MotorBus.read());
    if (c == '\r') {
      continue;
    }
    if (c == '\n') {
      handleCommand(rxLine);
      rxLine = "";
      continue;
    }
    if (rxLine.length() < 180) {
      rxLine += c;
    } else {
      rxLine = "";
      MotorBus.println("@0 ERR FRAME_TOO_LONG");
    }
  }
}

}  // namespace

void setup() {
  Serial.begin(kDebugBaud);
  delay(200);
  Serial.println();
  Serial.println("Motor ESP boot");

  esp_task_wdt_init(kTaskWatchdogTimeoutSec, true);
  esp_task_wdt_add(nullptr);
  serviceWatchdog();

  MotorBus.begin(kUartBaud, SERIAL_8N1, kMotorUartRxPin, kMotorUartTxPin);
  Serial.println("Motor UART gestartet RX=" + String(kMotorUartRxPin) + " TX=" + String(kMotorUartTxPin));

  pinMode(activeStepPin, OUTPUT);
  digitalWrite(activeStepPin, LOW);

  for (int i = 0; i < kStepperMotorCount; i++) {
    pinMode(kEnablePins[i], OUTPUT);
    digitalWrite(kEnablePins[i], HIGH);
  }

  pinMode(kDoorLockPin, OUTPUT);
  digitalWrite(kDoorLockPin, kDoorLockLockLevel);

  sendEvent("READY", "fw=motor-esp-v2");
}

void loop() {
  serviceWatchdog();
  pollMotorBus();
  completeDoorPulseIfDue();
}

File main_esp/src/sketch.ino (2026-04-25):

#include <Wire.h>
#include <hd44780.h>
#include <hd44780ioClass/hd44780_I2Cexp.h>
#include <Keypad.h>
#include <Preferences.h>
#include <SPI.h>
#include <SD.h>
#include <WiFi.h>
#include <WiFiClientSecure.h>
#include <HTTPClient.h>
#include <WebServer.h>
#include <Update.h>
#include <nvs_flash.h>
#include <esp_err.h>
#include <esp_system.h>
#include "mbedtls/sha256.h"
#include <time.h>
#include <memory>

#ifndef VM_ENABLE_LCD
#define VM_ENABLE_LCD 1
#endif

#ifndef VM_ENABLE_SD
#define VM_ENABLE_SD 1
#endif

#ifndef VM_ENABLE_WIFI
#define VM_ENABLE_WIFI 1
#endif

#ifndef VM_RGB_LED_PIN
#define VM_RGB_LED_PIN 48
#endif

// =====================================================
// Projekt Beschreibung
// Dieses Projekt steuert eines ESP32 S3 für einen Verkaufsautomaten.
// Der Verkaufsautomat hat aktuell folgende funktionen
// -Service Menü mit Wifi und Admin Pin Einstellungen
// -Webserver mit einfacher login oberfläche
// -steuern eines 4x4 keypads mit den Tasten 1-9 und *#ABCD
// =====================================================

// =====================================================
// Grundeinstellungen
// =====================================================
#define FW_VERSION "1.7.0"

hd44780_I2Cexp lcd;
bool lcdAvailable = false;
Preferences prefs;
WebServer server(80);

// =====================================================
// Keypad
// =====================================================
const byte ROWS = 4;
const byte COLS = 4;

char keys[ROWS][COLS] = {
  {'1', '4', '7', '*'},
  {'2', '5', '8', '0'},
  {'3', '6', '9', '#'},
  {'A', 'B', 'C', 'D'}
};

// ESP32-S3 Pinbelegung
byte rowPins[ROWS] = {10, 11, 12, 13};
byte colPins[COLS] = {14, 15, 16, 17};

Keypad keypad = Keypad(makeKeymap(keys), rowPins, colPins, ROWS, COLS);
const int keypadKeyCount = 16;
const char keypadRawKeys[keypadKeyCount] = {
  '1', '4', '7', '*',
  '2', '5', '8', '0',
  '3', '6', '9', '#',
  'A', 'B', 'C', 'D'
};
const char keypadSetupTargets[keypadKeyCount] = {
  '1', '2', '3', 'A',
  '4', '5', '6', 'B',
  '7', '8', '9', 'C',
  '*', '0', '#', 'D'
};
char keypadMappedKeys[keypadKeyCount + 1] = "147*2580369#ABCD";
bool keypadNeedsSetup = false;

// =====================================================
// App-Modi
// =====================================================
enum AppMode {
  MODE_NORMAL,
  MODE_SERVICE_PIN,
  MODE_SERVICE_MENU,
  MODE_INFO,
  MODE_WIFI_MENU,
  MODE_LANGUAGE_MENU,
  MODE_WIFI_EDIT_SSID,
  MODE_WIFI_EDIT_PASSWORD,
  MODE_WIFI_DHCP,
  MODE_WIFI_MANUAL_IP_MENU,
  MODE_WIFI_EDIT_IP,
  MODE_WIFI_EDIT_SUBNET,
  MODE_WIFI_EDIT_GATEWAY,
  MODE_WIFI_EDIT_DNS,
  MODE_ADMIN_PIN_MENU,
  MODE_ADMIN_PIN_ENTER_OLD,
  MODE_ADMIN_PIN_ENTER_NEW,
  MODE_ADMIN_PIN_CONFIRM_NEW
};

AppMode currentMode = MODE_NORMAL;

// =====================================================
// Texteingabe Zeichensätze
// =====================================================
enum TextCharSet {
  TEXTSET_UPPER,
  TEXTSET_LOWER,
  TEXTSET_NUM,
  TEXTSET_SYM
};

enum UiLanguage {
  LANG_DE,
  LANG_EN
};

// =====================================================
// Persistente Daten
// =====================================================
String adminPin = "12345678";

String wifiSSID = "";
String wifiPassword = "";
bool wifiDhcp = true;
String wifiManualIp = "192.168.1.50";
String wifiSubnet = "255.255.255.0";
String wifiGateway = "192.168.1.1";
String wifiDns = "8.8.8.8";
String wifiNtpServer = "pool.ntp.org";
bool emailNotifyEnabled = false;
String emailProtocol = "smtps";
String emailHost = "";
uint16_t emailPort = 465;
String emailUsername = "";
String emailPassword = "";
String emailFrom = "";
String emailTo = "";
uint8_t emailLowStockThreshold = 1;
UiLanguage currentLanguage = LANG_EN;
String currentCurrency = "EUR";

// =====================================================
// Laufzeitdaten
// =====================================================
String pinInput = "";
String tempNewPin = "";

String textBuffer = "";
String originalTextBuffer = "";

TextCharSet currentTextSet = TEXTSET_UPPER;
char activeMultiTapKey = '\0';
int activeMultiTapIndex = 0;
unsigned long lastMultiTapTime = 0;
const unsigned long multiTapTimeoutMs = 900;

// WiFi Status
bool wifiConnected = false;
String wifiStatusMessage = "Not connected";
unsigned long lastWifiAttemptMs = 0;
const unsigned long wifiRetryIntervalMs = 60000;
bool wifiStackInitialized = false;
bool timeSynced = false;
bool wifiSkipThisBoot = false;
bool wifiConnectPending = false;

// SD-Karte
const int sdCardSckPin = 39;
const int sdCardMosiPin = 40;
const int sdCardMisoPin = 41;
const int sdCardCsPin = 42;
SPIClass sdCardSpi(FSPI);
bool sdCardMounted = false;
String sdCardStatusMessage = "SD Karte nicht initialisiert";
const char* cashbookCsvPath = "/kassenbuch.csv";
const char* sumupLogPath = "/sumup.log";

// Webserver / Session
String webSessionToken = "";
bool webServerStarted = false;

// Firmware Update
struct FirmwareUpdateInfo {
  String version;
  String firmwareUrl;
  String sha256;
  String md5;
  String notes;
  uint32_t size;
  bool valid;
};

const char* firmwareUpdateManifestUrl = "https://sumup.kreativwelt3d.de/updates/main_esp/manifest.json";
const char* firmwareUpdateBaseUrl = "https://sumup.kreativwelt3d.de/updates/main_esp/";
FirmwareUpdateInfo cachedUpdateInfo = {"", "", "", "", "", 0, false};
String lastUpdateMessage = "";
String lastUpdateDetail = "";
unsigned long lastUpdateCheckMs = 0;
bool firmwareUpdateInProgress = false;

// Muenzpruefer
const int coinPulsePin = 18;
const uint8_t coinMappingMaxCount = 20;
const uint8_t coinDefaultMappingCount = 20;
uint8_t coinMappingCount = coinDefaultMappingCount;
uint8_t coinMappingPulses[coinMappingMaxCount] = {
  1, 2, 3, 4, 5,
  6, 7, 8, 9, 10,
  11, 12, 13, 14, 15,
  16, 17, 18, 19, 20
};
uint16_t coinMappingValuesCents[coinMappingMaxCount] = {
  100, 200, 300, 400, 500,
  600, 700, 800, 900, 1000,
  1100, 1200, 1300, 1400, 1500,
  1600, 1700, 1800, 1900, 2000
};
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

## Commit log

2026-04-18 improved readme and added 3d files
    [Door corner long Latch.stl, Sumup_Terminal+Solnoid.stl, Vendingmachine SumUp mod with 2 solnoid locks.3mf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]
2026-04-18 added readme for 3d printing files
2026-04-18 Added Motor ESP 3d Printing files
    [Back Stand_ESP32.stl, Back Stand_opto_DC-DC.stl, Keypad Body ESP32.stl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]
2026-04-18 updated location of files
    [Back Stand_ESP32.stl, Back Stand_opto_DC-DC.stl, Keypad Body ESP32.stl]
2026-04-18 added api bridge and motor esp wiring images in readme
2026-04-18 added BOM stub
2026-04-18 Added BOM entries
2026-04-18 updated bom
2026-04-18 changed Drivers in Motor Readme
2026-04-22 Readme and code improvements
    Added boot splash
    Added Keypad Usage in readme
    Added new flashing instructions
    Added LED indication of boot
    Added english language on first run
2026-04-23 update for I2C detection
2026-04-23 updated motor controller building script
2026-04-24 added more visual pictures for wiring the Steppers
